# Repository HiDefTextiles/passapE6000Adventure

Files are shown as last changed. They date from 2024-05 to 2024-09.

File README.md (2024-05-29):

# Passap gögn
Kortlagning í formi dagbóka færslna af samasöfnuðum gögnum fræa veraldar vefnum.

Það eru tvennir hugar í þessum heimi:
* Croucher og Knitterstream.
	*	Hlaða inn .cut skrám með hámarkslengd og breidd
	*	Interface svo við consolið til að ná automation
* Bamberg og Irene.
	*	Fjarlægja consolið og tengja allt í arduino
	*	Lesa staðsetningu frá ljósa skynjurum
	*	Stýra nálum sjálf með innbygðu seglunum
Sjá dagbók hér að neðan.

# Passap E6000

# 2/5/24

Samskipti helgu við Chris ofthestreet og
Annacroucher
## TODO, Hvað er?
* WinCrea
* KnitterStream
* DIN port
* Hvaða útgáfu erum við með?

<!-- `Creating our own circuit board, since arduino is too bulky and attaching that into the console` -->

### DIN port
Í tölvupóstasamskiptum er mynd þar sem sýnt er 6 pin DIN port.
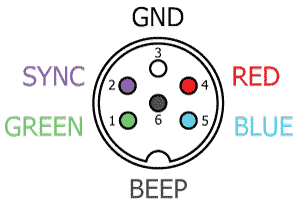
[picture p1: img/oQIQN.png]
Mynd af din 6 pin connector tengjum


### WinCrea
forrit til að gera hannanir fyrir Passap e6000 outputar .cut fileum sem er síðan hægt að h
### KnitterStream
* Notast við arduino til að interface við takka á stýringu.
* Hleður inn skrám eins og hægt er í chipset 23+ 

### Hvaða útgáfu erum við með?

Croucher vill að maður viti hvaða chipset vélin hefur en lýsingar til að komast að því eru óskýrar og krefjast jafnvel þess að rífa hana í sundur sem ég hef ekki leyfi fyrir enn.

## Chipset test
[Diana Natters umfjöllun um passap e6000](https://diananatters.blogspot.com/2010/10/passap-e6000-battery-chipset.html)

If it says MEMO, then start at step 1.

Þegar vélin er ræst kemur upp MEMO

Vélin öskrar og við fáum error 213.

Hún getur því ekki tekið við niðurhöluðum skrám.

## Croucher

Við erum með id 7041398 > 7037001.
Skv skjölum frá croucher eigum við því að vera með download og 32kb minni. En testið sem ég gerði frá diönu gaf error 213. Las yfir documentation fræa croucher aftur og hann seigir að error 213 sé rétt. Rámaði í það að ég hefði séð þessa tölu áður. Diana skrifar óskýrt en þetta er þá komið núna. Við erum með stuðning við að downloada patternum.

Það eru til mismunandi týpur af vélinni.
Það var bætt við download support frá MSDOS og auka minni í nýrri vélunum.
Það er hægt að uppfæra í það og kaupa frá honum íhluti til þess. Hann mæli eindregi með því að maður leggji ekki í það að uppfæra minnið og virðast ekki vera miklir kostir til þess.

Hægt er að hlaða niður skjölum, .cut sem innihalda
leiðbeiningar um lita munstur upp að 4 litum.
0,1,2,3
Leiðbeiningar um uppsetningar slíkar skrár eru í skjölum sem croucher sendi.

Það skjal inniheldur header með 10 stöfum og svo munstrið.

* Litafjölda stafur [0,3,4]: HEX[30,33,34] = [1-2,3,4] Litir
* Bil: HEX[20]
* Breidd munsturs/dálkar á bilinu [bil,bil,1] til [1,8,0]
* Bil
* Lengd munsturs/raðir á bilinu [bil,bil,1] til [2,5,5]
* Bil
* Litamunstur þar sem hver tala merkir lit 0-3

Hef það á tilfinningunni að við séum með eldri týpu annars væri ég ekki að lesa tölvupósta frá 2014.

## Irene
[Irene](https://hackaday.io/project/163701-passap-e6000-rebuilt-and-replaced-console/details)
[Irene repo](https://github.com/IrenePassap/Passap-E6000-hacked-and-rebuilt/blob/master/Passap_Projekt_Raspberry_Pi_Version_36.3_23.7.21.py)

Hún notar eina raspberry pi sem stýrir svo þrem arduino vélum. ein fyrir motor til að færa fram og til baka, ein fyrir fremri 'lock' til að prjóna og aðra fyrir aftari 'lock'.

Hún er búin að breyta vélinni þannig að aftara borðið er eins og fremra og getur þá líka prjónað eh meira fancy.

Hún vitnar í [bamberg](https://www.hackerspace-bamberg.de/Passap_pfaff_e6000)
.

Bamberg talar 'lightbarriers' í "carriage" til að vita staðsetninguna.

Finnst líklegt að við þurfum bara einfaldlega að losta okkur við upprunalgeu stýringuna eins og aðrir hafa gert. Þá kemur upp vandamál Croucher um að þú þarft í raun að forrita allt frá grunni með mikilli vitneskju um prjón og vélbúnaðinn.

## Niðurstöður // Summary

Erum með stuðning við að downloada .cut fileum.

Höfum 32k chip en 20k minni skv nýtni áætlun croucher.

Irene og bamberg hafa fjarlægt consolið gjörsamlega og smíðað sitt eigið með raspberry pi.

Ég held að við viljum halda consolinu og allri tækninni þar inni. grf.

Spurning um að bæta þá ofaná eh stýringu sem interfacer við consolið. Skoða knitterstream betur.

# 3/5/24

Byrjum á að skoða Irene og Bamberg betur.

* [Bamberg Github](https://github.com/knitty/firmware/tree/master/software/Knitty)
* [Bamberg lýsing (þýsk)](https://www.hackerspace-bamberg.de/Passap_pfaff_e6000)
* [Irene Github](https://github.com/IrenePassap/Passap-E6000-hacked-and-rebuilt)
* [Irene dagbók](https://hackaday.io/project/163701-passap-e6000-rebuilt-and-replaced-console/details)

## Diagram
### Bamberg

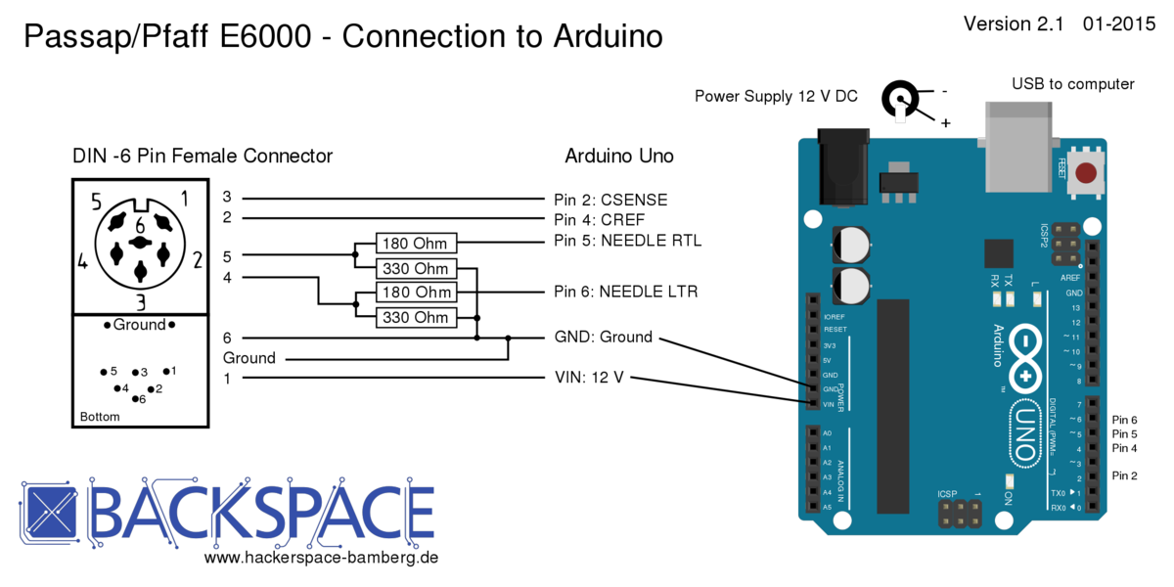
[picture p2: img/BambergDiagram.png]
BambergDiargram

Arduino unoinn kemur í stað stýringarinar 'consolsins' og notast þeir við sitt eigið forrit sem þeir gerðu fyrir alíka vél sem heitir [knitty](https://www.hackerspace-bamberg.de/Knitty)

Þeir eru líka með sér arduino fyror Autocolor, hvort hann hafi verið eh bilaður hjá þeim. Sé þetta ekki hjá Irene

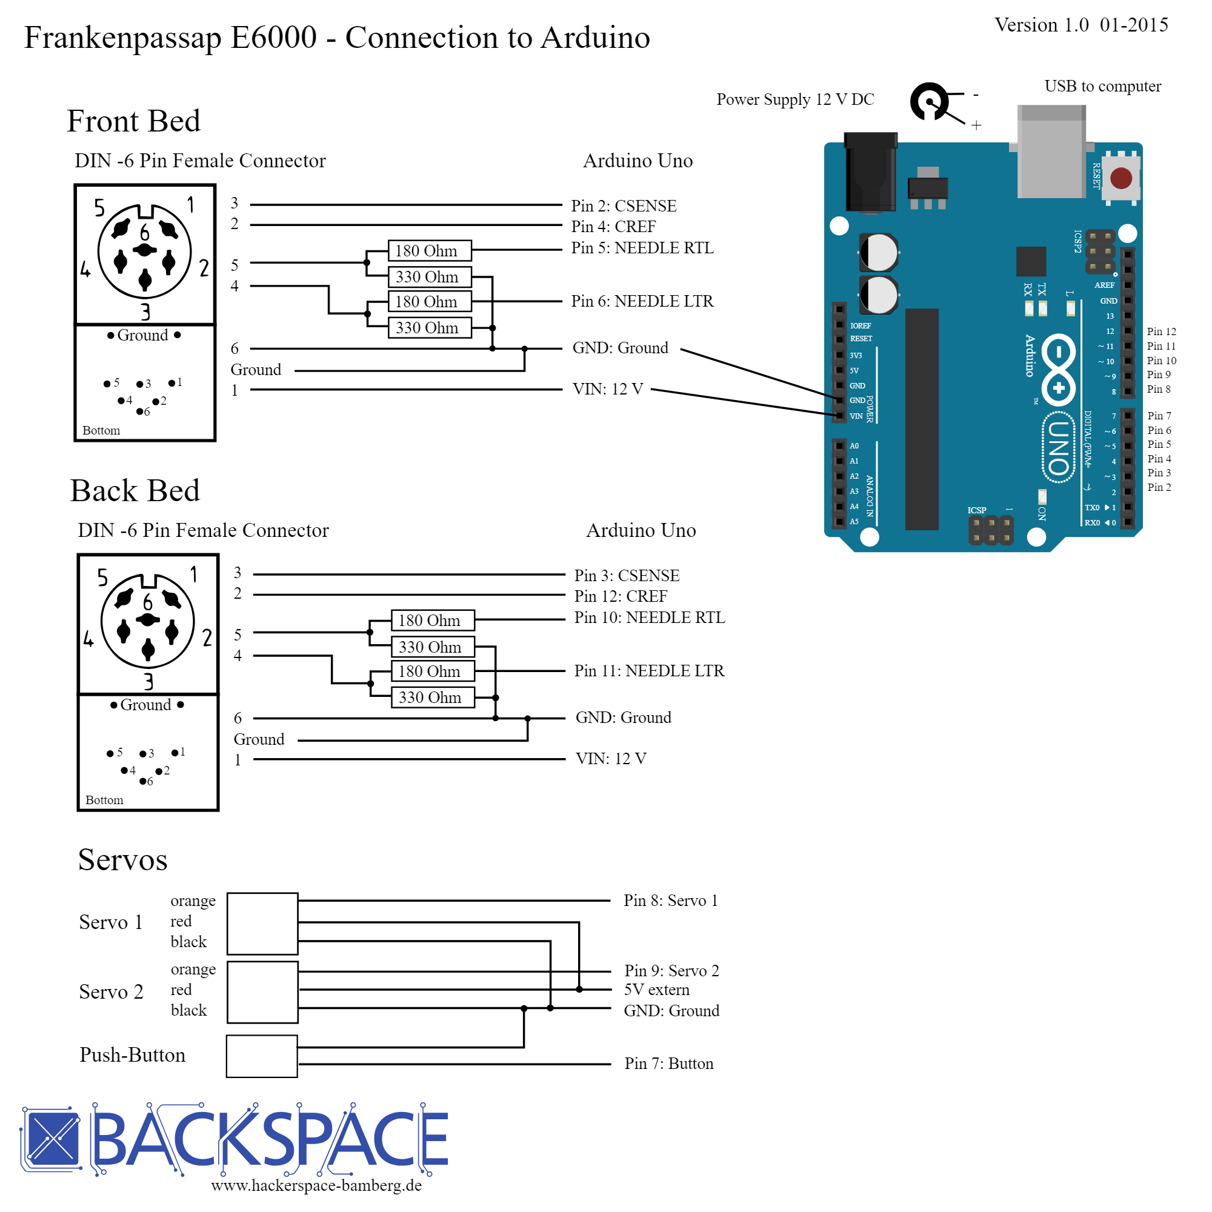
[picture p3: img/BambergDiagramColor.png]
mynd af tengingum við servo sem stýra litaskiptingum


[`Hægt er að sjá .svg diagram myndir frá Bamberg`](https://github.com/knitty/firmware/tree/master/hardware)

### Irene
IreneDiagram
Irene byggir á Bamberg en í stað þess að vera með tölvu usb tengda í arduino uno þá er raspberry pi með notendaviðmót sem stýrir

Lesa kóðan þeirra og skilja hvernig þau eru að lesa inn staðsetningu með pinum frá ljósunum. Þetta virðist ekki flókið en erfitt að ná hausnum almennilega utanum þetta án  þess að fikta sjálfur.
Mynd af seglum frá itene
<a href="https://hackaday.io/project/163701-passap-e6000-rebuilt-and-replaced-console/details" style="text-align:center;">Sjá meira hjá Irene</a>
Light sensorinn skýnir ljósi í 2mm göt á guiderail, 3mm á milli gata, 5mm er ein nál.

út frá munstri er hægt að lesa staðsetningu og átt lásins.

Ég bætti við Repoinu hennar Irene og bamber hér í möppu, til að auðvelda mér að fina efnið og rýna í það.

# 6/5/24

## Irene
Raspberry with two arduino sem stýra sitthvorum lásnum.
Hann stýrir svo mótornum. Það er ekkert samband á milli mótors og lása.

Mótorinn ýtir lásonum fram og til baka eins og ef noandi væri að gera það með hendinni og
lásarnir eru með ljós skynjara sem þeir nota til að lesa átt og staðsetningu.

Irene notast við technique.txt skrár fyrir gerð af prjóni?
Sva aðra skrá fyrir pattern.

Kóðarnir hennar eru torlesnir og gætu verið mun betur skrifaðir. Allar breytur eru global. Numpy er ekki notað fyrir fylki heldur forlykkju viðbjóður.

Ég tek það á mig að fara í gegnum þetta línu fyrir línu og endurskrifa allavega python kóðan uppá skilning fyrir mig. Besta leiðin til að skilja eitthvað er að laga það.

Þetta endar alltaf á því að maður þarf að fikta og prufa sig áfram.

Ég er búin að minnka fyrstu 800 línurnar niðu í minna en 200 með einfaldri notkun á numpy og skilning a fylkja notkun. Hægt er að sjá hreinskrifuðu útgáfuna undir möppunni Irene með nafninu controler-elli-cleanup.py

ég held áfram með þetta á morgun eftir hreinsun á vél

# 7/5/24

Þrif og teambonding

# 8/5/24

Punktar um gpio merki.

Til að fá gpio input í program er hægt að framkvæma "polling".
Getur misst af inputi ef gidli er lesið á vitlausum tíma.
Gert í lykkjum og er mögulega íþungt á keyrslu umhvefið.
Öunnr aðferðir er að nota "interrupts" sem tekur eftir muninum á milli breytingum, frá hi to low (falling) frá low to hi (rising)

Kláruðum að þrífa.

Skoðaði betur munninn á tölvu og mekanísku útgáfunni frá Passap.

Tölvu útgáfan er með 
- 2 input, ljósskynjararnit tveir sem staðsetjan
- 2 output, seglar sem raða nálum fyrir munstur næstu línu
Sameiginlegt er
- Mekaníkinn sem ýtir nálonum upp er sú sama.
- nálabeðið er óbreytt

# 10/5/24

Öll ljós slökkt og ekki sál að sjá.

Er komin með 250 línur af hreinskrifaðari kóða útgáfu frá Irene.

Er að bryja á tech array hjá henni.

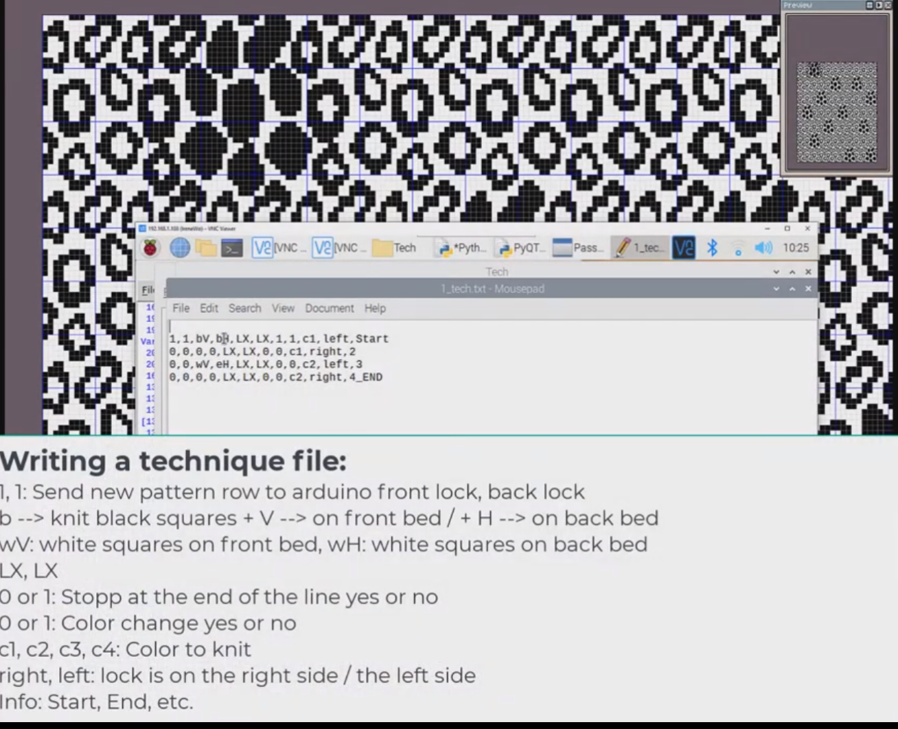
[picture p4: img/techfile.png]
Mynd af tech array dæmi


Hér útskýrist betur þessi blessaði tech array file hjá henni.

fyrstu tvö gildin lýsir hún sem skipun um að byrja pattern á nýrri línu.

```
    x = tech_Array[countTech][0]
    x = int(x)
    rowCount_VNB = int(rowCount_VNB) + x
```

Þar sem rowcount_VNB er nr línu á fremri lásnum.
countTech er lína í tech file, 0 er index á fyrstu tölunni

Næst koma hvaða lita vigra hún nota.
Þar er gefin strengur sem er enumaður á skipun sem sendir viðeigandi vigur á viðeigandi Arduino.

V - fremri, H - Aftari

Svo er stillingin sem að lásin á að vera í. Hún stilir það sjálf

svo skipanir til að skipta um lit, sem ég skil ekki alveg.

Hún seigir að þetta sé boolean já og nei fyrir skipti og stop en þegar hún skiptir um lit breytast þesssi gildi ekki neitt.

svo bara info dump, þetta væri vel hægt að sleppa.

Virkni segla lásins voru í raun sanreynd í prufunum í dag. 
Hann stillit uppröðunninni fyrir næstu umferð. Default er 1 þarf að senda 0 til að setja í hvildarstöðu.
Pusherarnir stýra svo einhvernveginn hvaða nálar eru notaðar.
Það er bara hlustað á pusherana þegar x stilling er virk og þegar kveikr er á örvum í gömlutýpunni er uppröðun þeirra breytt.

Þetta væri þá hægt að þýða yfir í kóða og sleppa motor stýringum.

Prufurnar gengu þó eh og gott að sjá mekaníkinn í virkni.

# 15/5/24

## Prototype 1

Staðan í dag, komin með arduino tengingu við lásinn. Get lesið ljósskynjara og breytt segulsviði seglana.

Þá er bara að stúttera bamberg og irene stýringarnar.

Næ að láta intterupt virka fyrir PIN_CSENSE en ekki PIN_CREF, en hann skynjar breytt gildi á báðum þannig við látum eina innterrupt rútínu virka

Fyrir Vinstri til hægri koma gildin

40 & 31

Fyrir hægri til vinstri fáum við gildin

41 & 30

Úr innterrupt rútinum hennar Irene

# 16/5/24

## Prototype 2
Ný rás fræsuð, viðnám lóðuð, tengi og pinnar.

Skynjarar í lagi, skipti út powersupply fyrir annað sem ég fann liggjandi í vr 3 og seglarnir virka.

Þá er bara eftir að útfæra kóða sem samnýtir hreyfingu

# 17/5/24

CREF er ekki tengt í pinna sem styður interrupt.

Vélin stíflaðist, tók hana í sundur, sem er fínt. Hafði langað að gera það til að sjá pusherana betur.

# 21/5/24

Horfði upp undir pusherana til að sjá hvar þeir byrja að raðast eftir stillingu. Breytti svo stillingunni og sá hversu margir pusherar voru á milli þess að breytinginn skilaði sér. Merkti þann punkt á velina og notaði hann sem calibration punkt.

Þetta er punkturinn þar sem röðun pusherana er ákveðin. Hvort þeir fara upp eða niður. Miðaði svo við þann punkt og prófaði að færa hann eitt nálarbeð í einu og breyta stillingu til að sannreyna og það gekk. 

Notaði svo ljósaskynjarann og las hvaða munstur kom úr interruptinu í hvert skipti sem ég færði calibration/samstillingar punktinn á milli nálarbeða. 

Tölugildin eru því 41 og 31 eða 11 og 01;
11: Cref=1 & Csense=1;
01: Cref=0 & Csense=1;

Til að staðsetja lásin á nálarbeðinu tökum við hann alveg út í enda. Rennum honum svo hægt inná leiðarvísirinn og greinum gildi.

Út frá því fáum við alla punkta. Það ætti að vera nóg að gera þetta bara í eina átt. Frá vinstri til hægri, horft beint á fremri lásin. Því Hægri til vinstri ætti í raun bara að telja niður sömu gildi, allavega fyrir nálarbeðin, jaðar punktarnir gætu verið annað mál. SKoðum það þegar þar að kemur

Punktar fyrir kvörðun á nálabeða ás útfrá ljósskynjara

Upphafsgildi breyturnar state & counter eru 0;
```
// direction
volatile int state = 0;
// position
volatile int counter = 0;
```

State seigir okkur um stöðu beggja ljósskynjarana og útfrá því getum við ákvarðað átt. Counter telur hverja nál og er ætlað til að staðsetja okkur.

Með state ákvöðrum við hvort við hækkum eða lækkum counter, út frá counter fáum við staðetningu

# 22/5/24

Villur lagaðar og ás nálabeðs kvarðaður.

Til að kvarða nálabeðið þarf að taka lásinn/sleðann af. Endurkveikja á arduino og renna honum á.

// 30 0
// 31 0

// 31 0
// 40 -1
// 41 0
// 40 -1
// 41 0
// 40 -1

// byrjar 31 0
// svo mynztur 40 - 41
// byrjar loks 41 - 30
// í 28 erum við komin á fyrstu nálina
// 207 seinasta nál || 206
// 243 auto color endir
// 221 útaf hægri

# 23/5/24

Munztrið sem kemur þegar honum er rennt á er, 40 telur niður og 41 upp

31 - 0
40 - -1
41 - 0
40 - -1
41 - 0
40 - -1
41 - 0 // 41-30 nála munustur++
30 - 0
41 - 1

28 er nál 1 og 206 nál 179

## Kenning 

Nálabeðið er samhverft og merkt með heiltölum í báðar áttir frá miðju með 

90 nálar vinstra megin

89 nálar hægra megin

Tölvur byrja í núlli, þannig ef fyrsta nálinn vinstra megin við miðju er 0
þá er nálabeðið samhverft um hana í hugbúnaðinum það er

-89 0 89.

## Framkvæmd

Við viljum að notandinn geti skilgreint fyrstu nál til vinstri. Best væri að notandinn gæti notast við innbygpu tölurnar á vélinni.

Notandi segir að munztur byrji á nál 90 til vinstri, þá þarf það að vera 0 í munztur vigri.

setur inn -90,
sem er nál 28
### Hugmynd
```
int input = -90;
int start = (input < 0) ? input +90 : input + 89;
int line = 0;
counter - 28 - (start) = 0;
206 - 28 = 179
if (counter >= (28+start) && counter < 207)
{
	int index = counter - 28 - start;
	digitalWrite(pin,PatternMatrix[index])
	if (counter > width of matrix + start || (line>0 && counter < 28+start))
	{
		line++
	}
}

counter - 28 + input = 0
```

### útfærsla
Notobene þetta eru 178 nálar og við byrjum í 0,
þannig index er á bilinu 0-177, fyrir allar nálar á borðinu

#### Einn vídd Index
```
    int input = -90;
    int start = (input < 0) ? input + 90 : input + 89;
    int index = counter - 28 - start;
```
If var óþarfi þar sem við setjum bara núll punkt og okkur ætti að vera sama um öll önnur gildi. Þannig þótt index flæði út fyrir þá er hann ekki að stýra neinu.

Þegar ég var að prufukeyra index, var ljost að þar sem seglarnir eru ekki á samastað þá þarf að vera með sér tölu fyrir hvorn, það virðist vera 10 nála bil á milli, þannig við bara bætum við 10 á bakaleiðinni við index. einnig virtist vera 2 nála offset frá fyrstu nál og stillingar punkti, sem er innan skekkju marka mannsins.

vona ég.

ég breytti því núll punkti nálarásins í 26 til að lagfæra það.

```
		int input = -10;
		int start = (input < 0) ? input + 90 : input + 89;
		int index = counter - 26 - start;
		int value = 1;
```
##### Hægri til vinstri
```
			if (index + 10 >= 0 && index + 10 < arraysize)
			{
				value = array[index + 10];
			}
			digitalWrite(PIN_NEEDLE_RTL, value);
```
##### Vinstri til hægri
```
			if (index >= 0 && index < arraysize)
			{
				value = array[index];
			}
			digitalWrite(PIN_NEEDLE_LTR, value);

```
#### Tveggja vídda Index
Þá er það línu meðhöndlun.

Byrjum alltaf að prjóna hægri til vinstri.
Setjum alltaf lásinn/sleðann á frá vinstri til hægri.

Þurfum þá að stilla nálarnar þannig fyrst.

Þannig sleðin byrjar alltaf lengst til vinstri?
vonandi

# 27/5/24

Fann kennslumyndbönd á netinu um það hvernig maður sendir skipanir frá python yfir á arduino.

## Næstu ítranir // TODO
- Útfæra grunn að samskiptum á milli arduino og umheimsins
	- Bæta við raspberry pi
	- bakenda
	- python/javascript?
- Bæta við motor // skoða
	- mögulega motor stýringu
	- Hægt að vita staðsetningu autocolor

# 28/5/24

Takmarkanir á gögnum send til arduino.

Ef við notum streng þá getur hann verip með 768 stafi.

Ef við sendjum

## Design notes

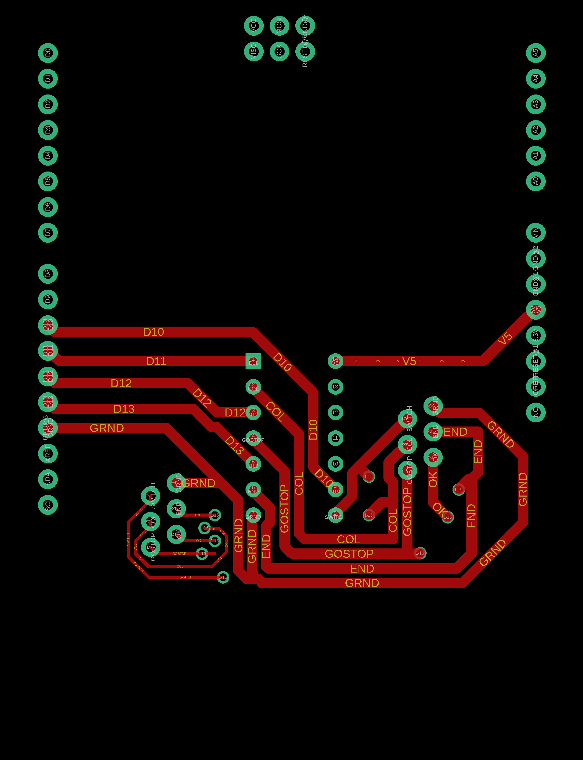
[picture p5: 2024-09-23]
teikningarRaf/Passap/PASSAP_MOTOR_ARDUINO.png

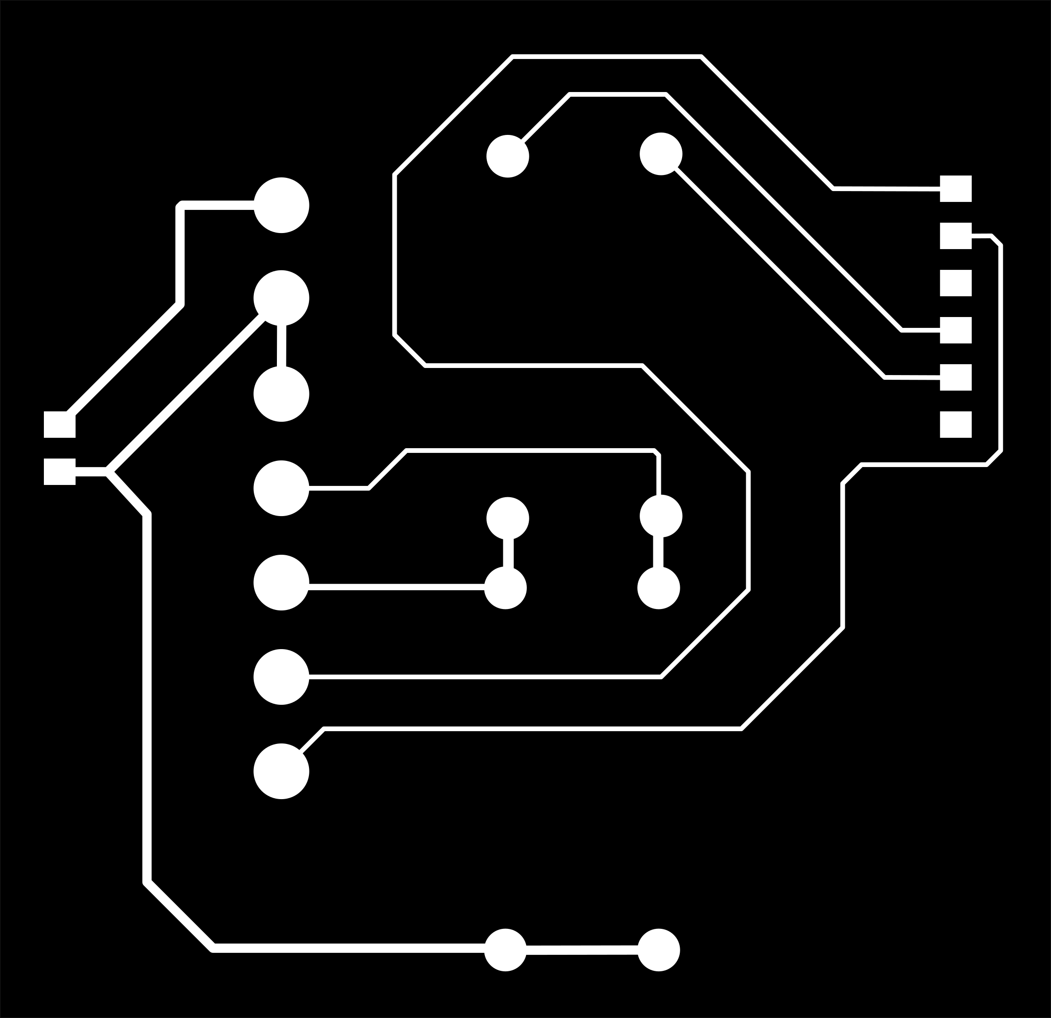
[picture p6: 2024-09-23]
teikningarRaf/svgdot/Traces.png

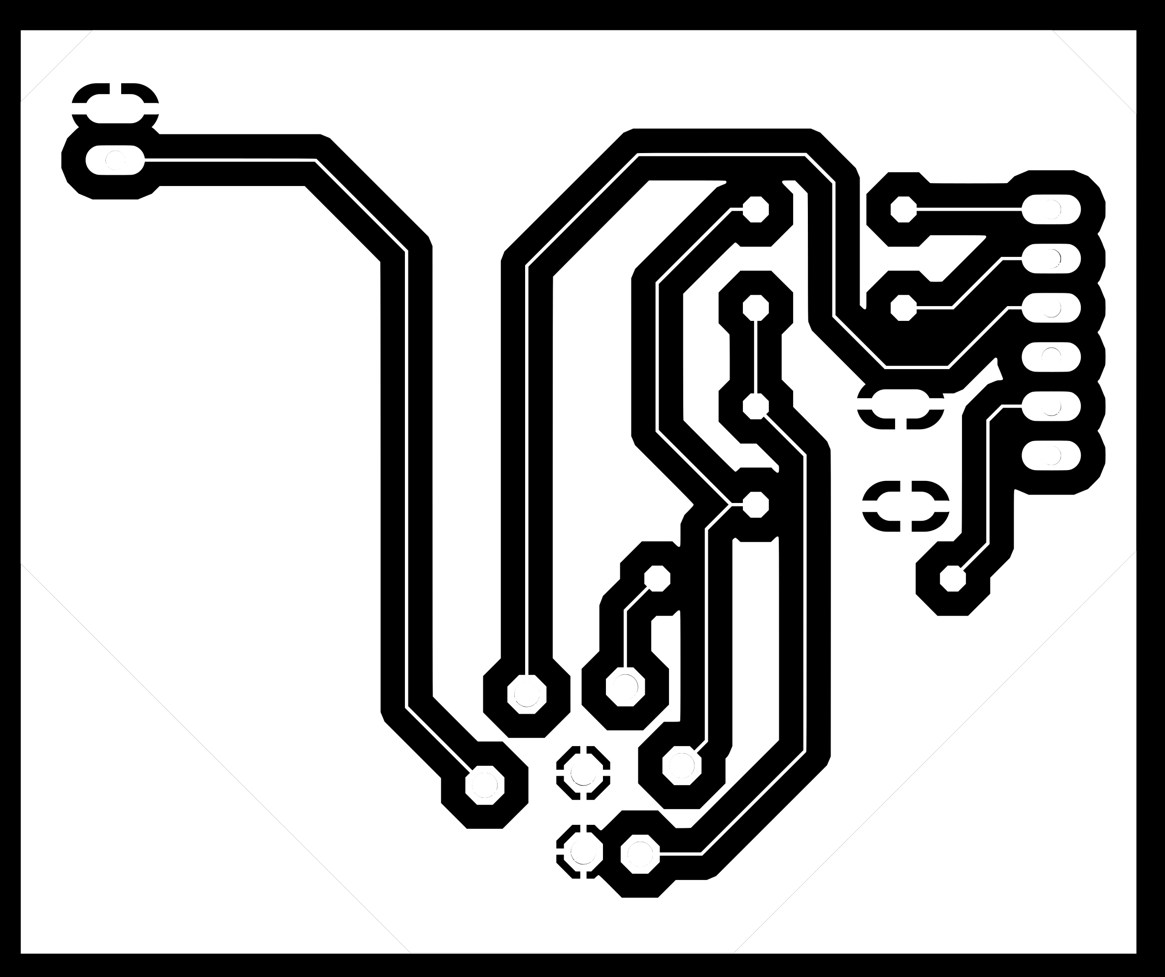
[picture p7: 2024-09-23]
teikningarRaf/svgdot/Traces_Thundercat.png

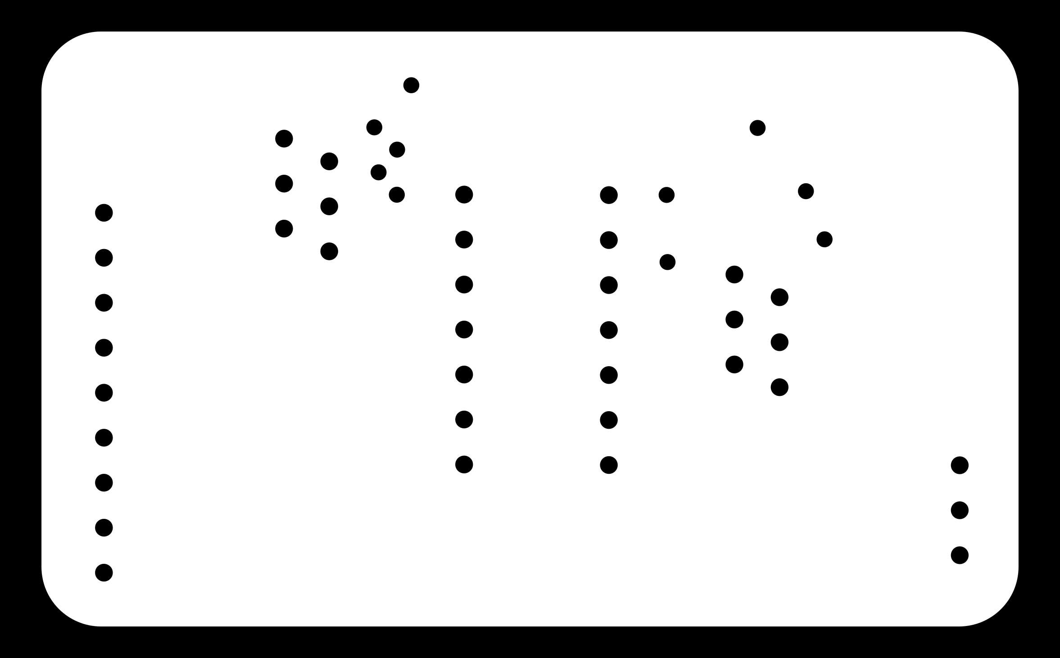
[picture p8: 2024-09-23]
teikningarRaf/svgdot/PassapMotorOutline1_flip.png

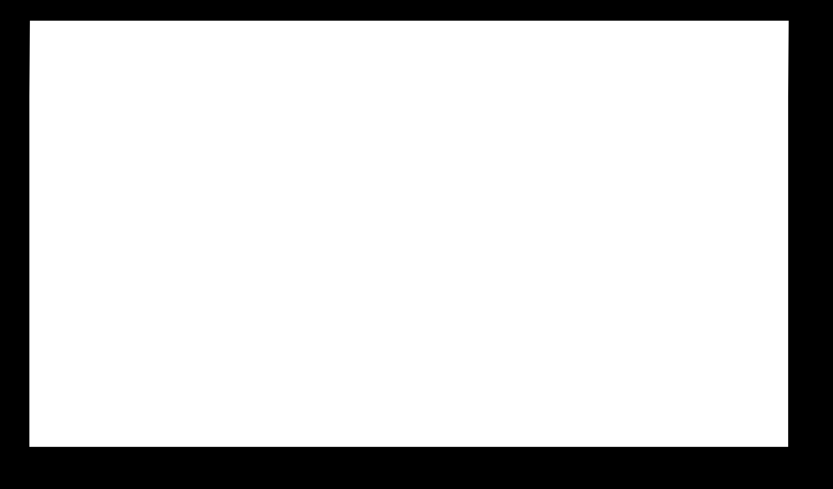
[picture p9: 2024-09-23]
teikningarRaf/svgdot/passapMotorKassi.png

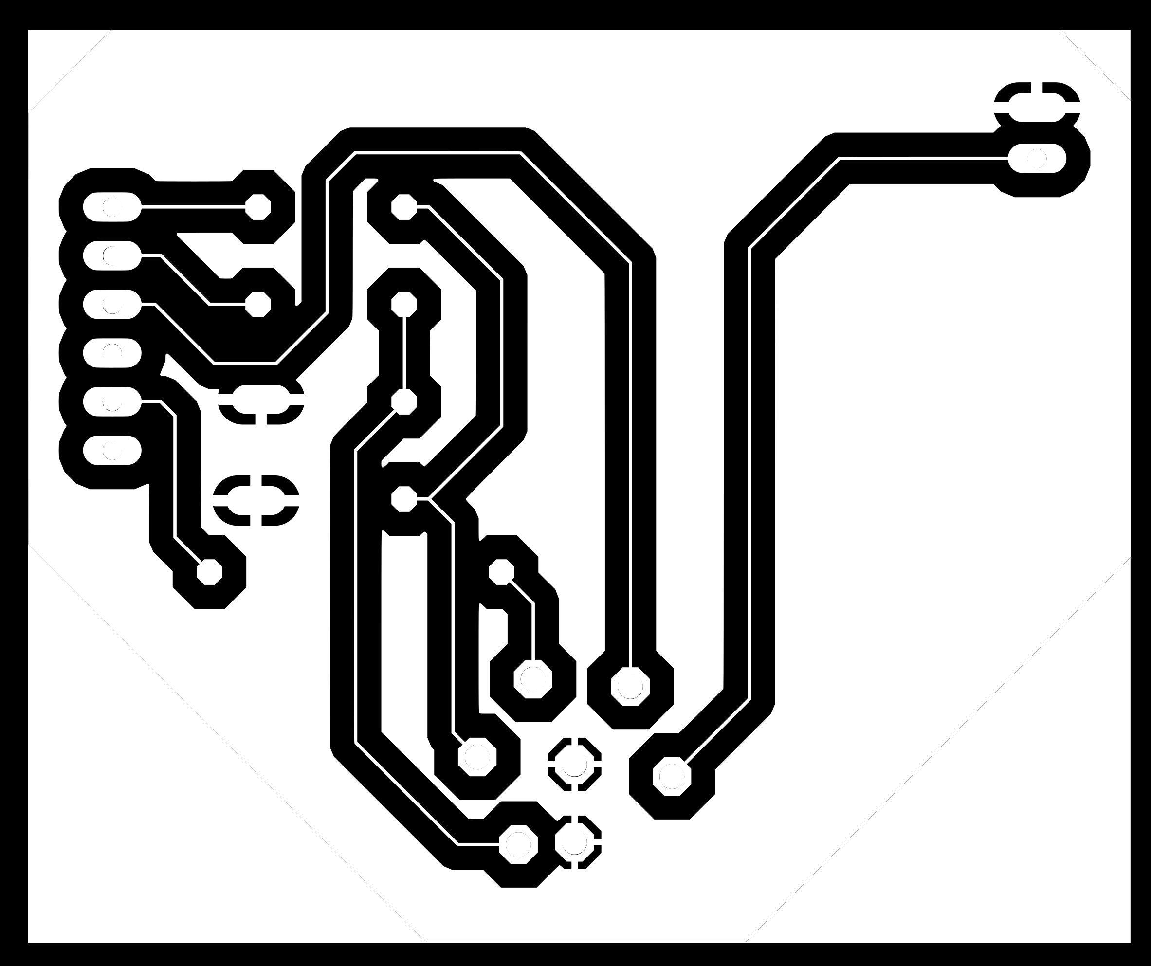
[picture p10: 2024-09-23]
teikningarRaf/svgdot/Traces+thundercat1.png

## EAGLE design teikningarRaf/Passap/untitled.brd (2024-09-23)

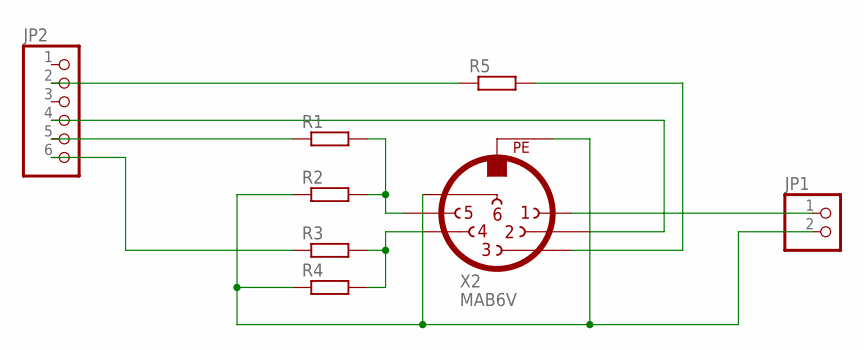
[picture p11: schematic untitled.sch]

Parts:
JP1: PINHD-1X2; 1X02
JP2: PINHD-1X6; 1X06
R1, R2, R3, R4: R-EU_0204/7; 0204/7
R5: R-EU_0207/15; 0207/15
X2: MAB6V

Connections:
GND: JP1.2, R2.1, R4.1, X2.6, X2.PE
unnamed: R1.2, R2.2, X2.5
unnamed: R3.2, R4.2, X2.4
unnamed: R5.2, X2.3
unnamed: JP2.5, R1.1
unnamed: JP2.6, R3.1
unnamed: JP2.4, X2.2
unnamed: JP2.2, R5.1
unnamed: JP1.1, X2.1

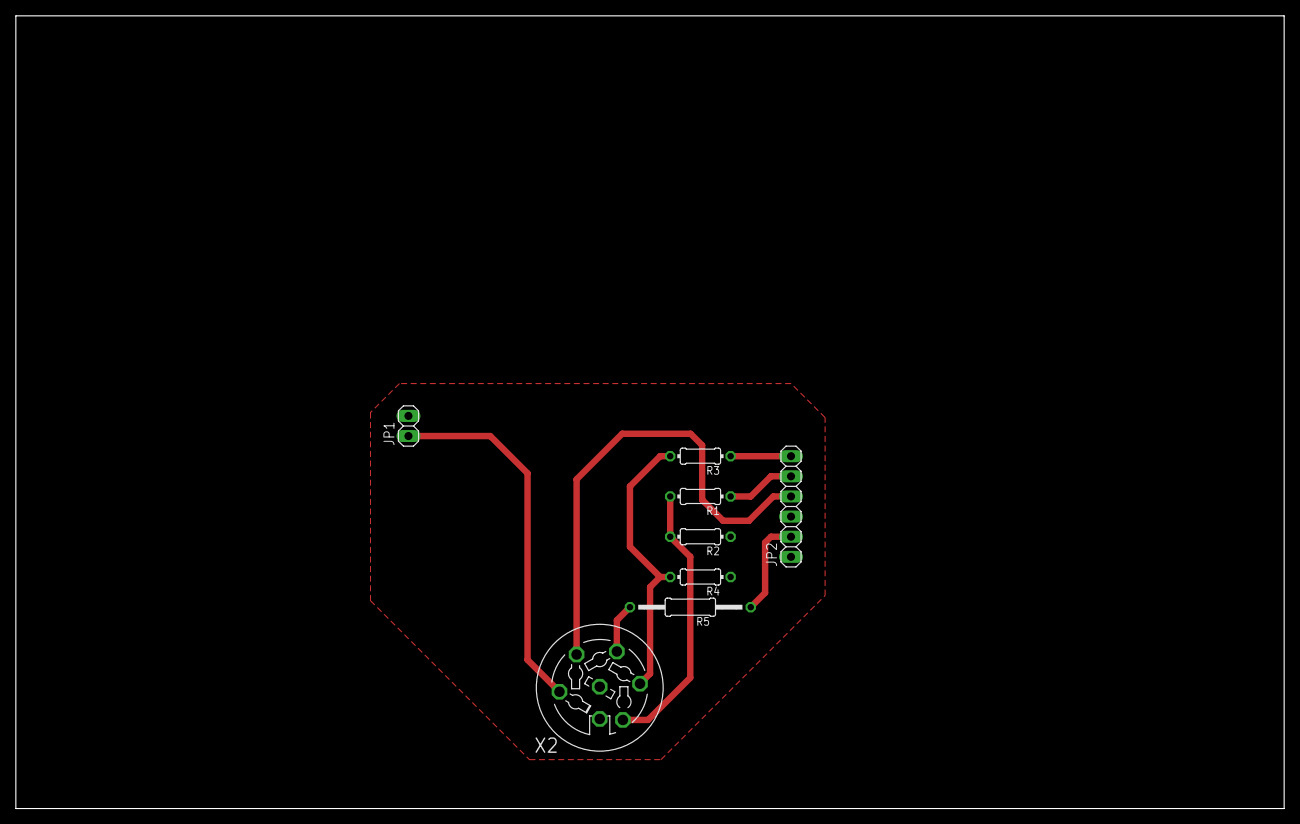
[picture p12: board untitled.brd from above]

Board: 2 copper layers, 160.0 x 100.0 mm, 8 parts (0 on the bottom side), 9 nets.

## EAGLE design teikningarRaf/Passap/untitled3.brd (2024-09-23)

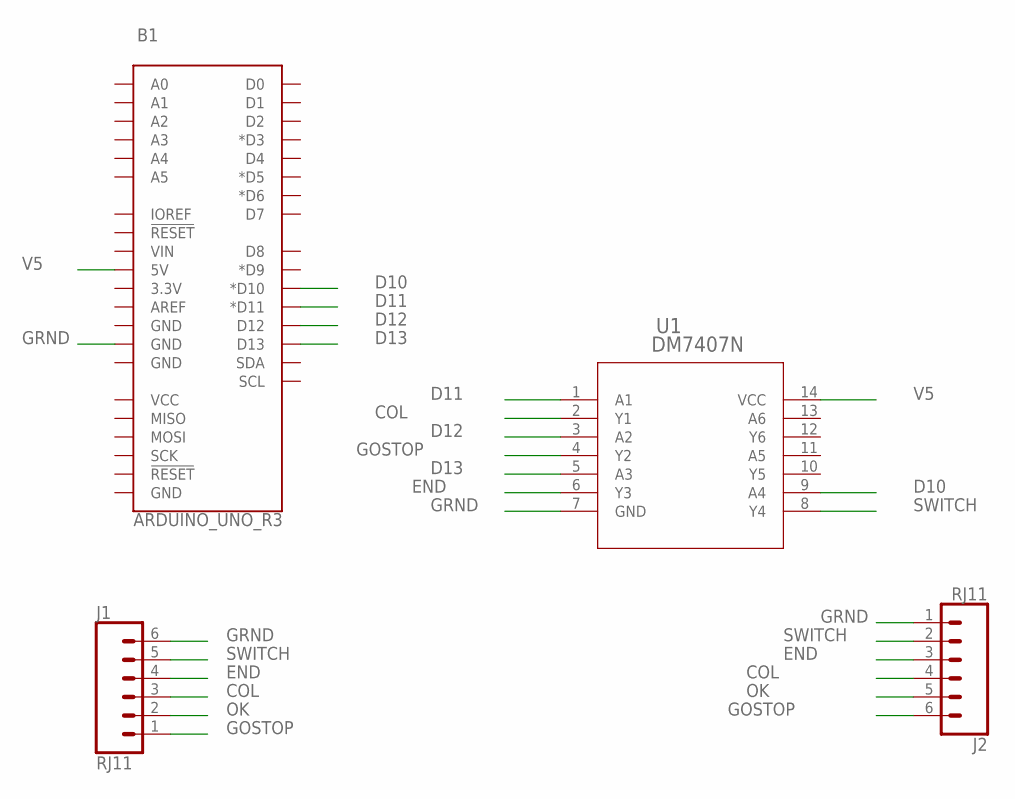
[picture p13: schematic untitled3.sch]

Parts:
B1: ARDUINO_UNO_R3; ARDUINO_R3
J1, J2: RJ11; RJ11-6
U1: DM7407N; PDIP14_6P35X19P56_ONS

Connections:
COL: J1.3, J2.4, U1.2 (Y1)
D10: B1.D10 (*D10), U1.9 (A4)
D11: B1.D11 (*D11), U1.1 (A1)
D12: B1.D12, U1.3 (A2)
D13: B1.D13, U1.5 (A3)
END: J1.4, J2.3, U1.6 (Y3)
GOSTOP: J1.1, J2.6, U1.4 (Y2)
GRND: B1.GND@3 (GND), J1.6, J2.1, U1.7 (GND)
OK: J1.2, J2.5
SWITCH: J1.5, J2.2, U1.8 (Y4)
V5: B1.5V, U1.14 (VCC)

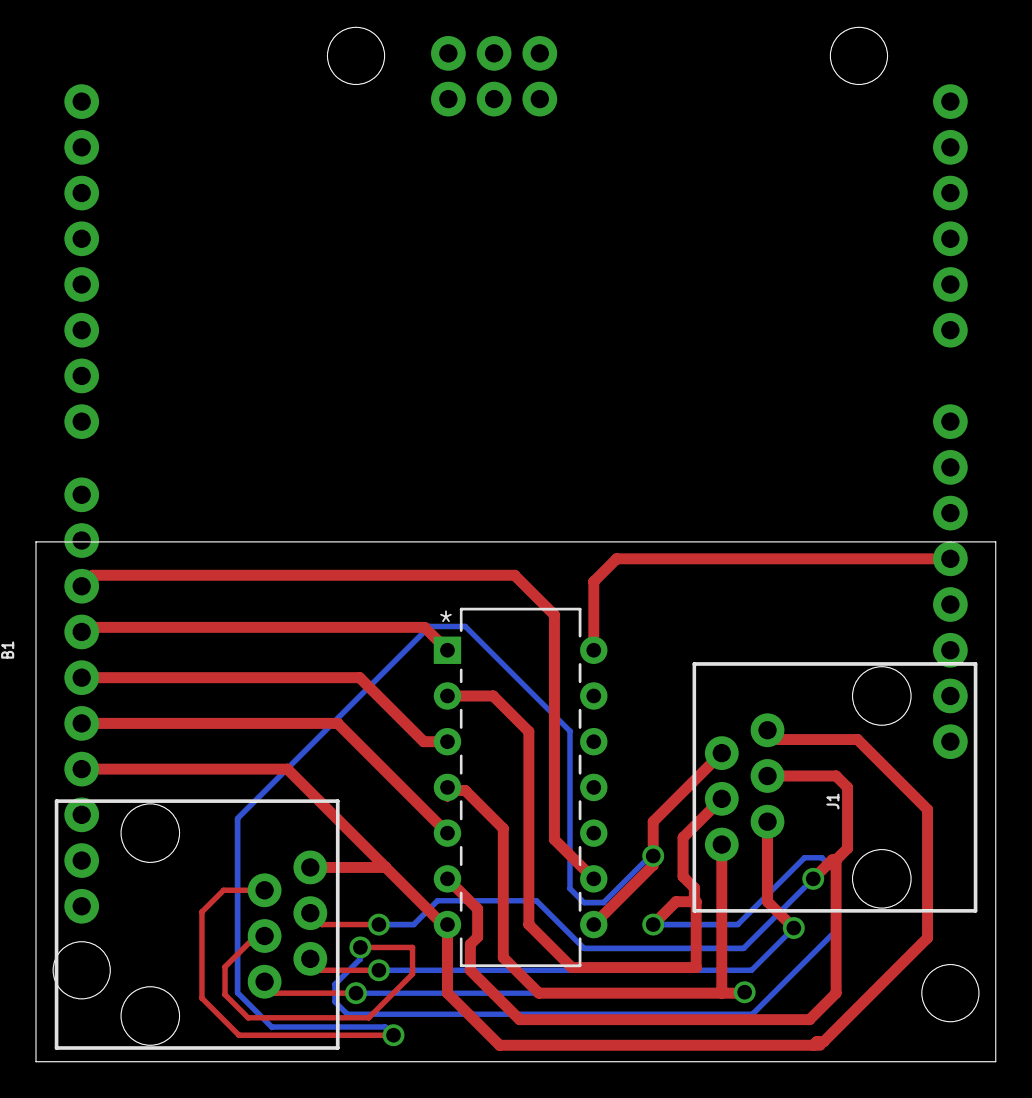
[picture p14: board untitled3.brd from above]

Board: 2 copper layers, 53.3 x 28.9 mm, 4 parts (0 on the bottom side), 11 nets.

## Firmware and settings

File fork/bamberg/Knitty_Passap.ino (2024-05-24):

//////////////////////////////////////////////////////////////////////////////
// Knitty Project
// Arduino Firmware for Passap E6000
//
// Author: ptflea, schinken,
//
// version 2015-10-05

// Servo
#include <Servo.h>

Servo servoColour12; // create servo object to control a servo
Servo servoColour34;

// define interupts for CSENSE
#define INT_ENCODER 0
#define INT_ENCODER_BACK 1

//////////////////////////////////////////////////////////////////////////////
// General purpose definitions

// front carriage
#define PIN_CSENSE 2     // Yellow
#define PIN_CREF 4       // White
#define PIN_NEEDLE_RTL 5 // Blue,  Pattern RTL
#define PIN_NEEDLE_LTR 6 // ,  Pattern LTR
// back carriage
#define PIN_CSENSE_BACK 3      //
#define PIN_CREF_BACK 12       //
#define PIN_NEEDLE_RTL_BACK 11 //   Pattern RTL
#define PIN_NEEDLE_LTR_BACK 10 //   Pattern LTR

// PIN 8 and 9 are for the color change servos

#define DIRECTION_UNKNOWN 0
#define DIRECTION_LEFT_RIGHT -1
#define DIRECTION_RIGHT_LEFT 1

#define DIRECTION_UNKNOWN_BACK 0
#define DIRECTION_LEFT_RIGHT_BACK -1
#define DIRECTION_RIGHT_LEFT_BACK 1

char currentDirection = DIRECTION_UNKNOWN;
char lastDirection = DIRECTION_UNKNOWN;
char currentDirection_back = DIRECTION_UNKNOWN;
char lastDirection_back = DIRECTION_UNKNOWN;

signed int currentCursorPosition = 0;
unsigned long lastCursorChange = 0;
unsigned int currentPatternIndex = 0;
signed int firstNeedle = 0;
signed int offsetCarriage_RTL = 53;
signed int offsetCarriage_LTR = 29;

signed int currentCursorPosition_back = 0;
unsigned long lastCursorChange_back = 0;
unsigned int currentPatternIndex_back = 0;
// signed int firstNeedle_back = 0;
signed int offsetCarriage_RTL_back = 50;
signed int offsetCarriage_LTR_back = 27;

int knitPattern[255] = {0};
int knitPattern_back[255] = {0};

int passapCalibrateArray[8] = {0};
signed int passapCalibratePointer = 0;
static unsigned char passaptestpattern[8] = {1, 0, 1, 1, 0, 0, 0, 1};

int passapCalibrateArrayBack[8] = {0};
signed int passapCalibratePointerBack = 0;
static unsigned char passaptestpatternBack[9] = {0, 0, 1, 1, 1, 0, 1, 1, 0};

char currentPinChangeValue = 0;
char currentPinChangeOppositeValue = 0;
char currentPinChangeValue_back = 0;
char currentPinChangeOppositeValue_back = 0;
signed int currentCursorPositionLast = 0;
signed int currentCursorPositionLast_back = 0;
//////////////////////////////////////////////////////////////////////////////
// Knitty Serial Protocol

// Receive commands
#define COM_CMD_PATTERN 'P'
#define COM_CMD_PATTERN_BACK 'B'
#define COM_CMD_PATTERN_END 'E'
#define COM_CMD_CURSOR 'C'
#define COM_CMD_RESPONSE 'R'
#define COM_CMD_DIRECTION 'D'
#define COM_CMD_DEBUG 'V'
#define COM_CMD_NEW_PATTERN 'N'
#define COM_CMD_FIRST_NEEDLE 'F' // first needle of pattern from right
#define COM_CMD_SEPERATOR ':'
#define COM_CMD_STATUS 'T'

#define COM_CMD_SERVO 'S'

#define COM_CMD_PLOAD_END '\n'

// Parser states
#define COM_PARSE_CMD 0x01
#define COM_PARSE_SEP 0x02
#define COM_PARSE_PLOAD 0x03

unsigned char parserState = COM_PARSE_CMD;

unsigned char parserReceivedCommand = 0;
String parserReceivedPayload = "";
unsigned char patternLength = 0;
unsigned char patternLengthBack = 0;

void setup()
{
  Serial.begin(115200);
  sendCommand(COM_CMD_RESPONSE, "up and running");

  // Setup PHOTO SENSOR pin change interrupt
  pinMode(PIN_CSENSE, INPUT_PULLUP);
  pinMode(PIN_CSENSE_BACK, INPUT_PULLUP);

  pinMode(PIN_CREF, INPUT_PULLUP);
  pinMode(PIN_CREF_BACK, INPUT_PULLUP);

  attachInterrupt(INT_ENCODER, interruptPinChangeEncoder, CHANGE);
  attachInterrupt(INT_ENCODER_BACK, interruptPinChangeEncoder_back, CHANGE);

  // Setup Needles
  pinMode(PIN_NEEDLE_RTL, OUTPUT);
  digitalWrite(PIN_NEEDLE_RTL, HIGH);
  pinMode(PIN_NEEDLE_LTR, OUTPUT);
  digitalWrite(PIN_NEEDLE_LTR, HIGH);

  pinMode(PIN_NEEDLE_RTL_BACK, OUTPUT);
  digitalWrite(PIN_NEEDLE_RTL_BACK, HIGH);
  pinMode(PIN_NEEDLE_LTR_BACK, OUTPUT);
  digitalWrite(PIN_NEEDLE_LTR_BACK, HIGH);
}

void loop()
{
  parserSerialStream();
  patternFront();
  patternBack();
}

void executeCommand(unsigned char cmd, String payload)
{

  switch (cmd)
  {
  case COM_CMD_PATTERN:
    // Serial.print("P ");
    // Serial.println(patternLength);
    //  sendCommand(COM_CMD_RESPONSE, "PatternLength: " + String(patternLength));
    break;

  case COM_CMD_PATTERN_BACK:
    // Serial.print("B ");
    // Serial.println(patternLengthBack);
    // sendCommand(COM_CMD_RESPONSE, "PatternLengthBack: " + String(patternLength));
    break;

  case COM_CMD_CURSOR:
    currentCursorPosition = payload.toInt();
    break;

  case COM_CMD_FIRST_NEEDLE:
    firstNeedle = payload.toInt() * 2 - 2;

    sendCommand(COM_CMD_RESPONSE, "FirstNeedle: " + String(firstNeedle));
    break;

  case COM_CMD_STATUS:
    sendCommand(COM_CMD_RESPONSE, "-------------------------");
    sendCommand(COM_CMD_RESPONSE, "Cursorposition: " + String(currentCursorPosition));
    sendCommand(COM_CMD_RESPONSE, "PatternIndex: " + String(currentPatternIndex));
    if (currentDirection == DIRECTION_RIGHT_LEFT)
    {
      sendCommand(COM_CMD_DIRECTION, "RTL");
    }
    else
    {
      sendCommand(COM_CMD_DIRECTION, "LTR");
    }
    sendCommand(COM_CMD_RESPONSE, "-------------------------");

    break;

  case COM_CMD_SERVO:

    switch (payload.toInt())
    {
    case 0: // no colour selected
      servoColour12.write(90);
      servoColour34.write(90);
      break;
    case 1: // Color 1
      servoColour12.write(70);
      servoColour34.write(90);
      break;
    case 2: // Color 2
      servoColour12.write(115);
      servoColour34.write(90);
      break;
    case 3: // Color 3
      servoColour12.write(90);
      servoColour34.write(70);
      break;
    case 4: // Color 4
      servoColour12.write(90);
      servoColour34.write(115);
      break;
    case 5: // Servo off
      servoColour12.detach();
      servoColour34.detach();
      break;
    case 6: // Servo on
      servoColour12.attach(8);
      servoColour34.attach(9);
      break;
    }

    break;
  }
}

void sendCommand(unsigned char cmd, String payload)
{
  Serial.write(cmd);
  Serial.write(COM_CMD_SEPERATOR);
  Serial.print(payload);
  Serial.write("\n");
}

void parserSerialStream()
{

  if (Serial.available() == 0)
  {
    return;
  }

  char buffer = Serial.read();

  switch (parserState)
  {

  case COM_PARSE_CMD:
    parserState = COM_PARSE_SEP;
    parserReceivedCommand = buffer;
    parserReceivedPayload = "";
    if (buffer == COM_CMD_PATTERN)
    {
      patternLength = 0;
    }

    if (buffer == COM_CMD_PATTERN_BACK)
    {
      patternLengthBack = 0;
    }
    break;

  case COM_PARSE_SEP:

    // We're awaiting a seperator here, if not, back to cmd
    if (buffer == COM_CMD_SEPERATOR)
    {
      parserState = COM_PARSE_PLOAD;
      break;
    }

    parserState = COM_PARSE_CMD;
    break;

  case COM_PARSE_PLOAD:

    if (buffer == COM_CMD_PLOAD_END)
    {

      executeCommand(parserReceivedCommand, parserReceivedPayload);
      parserState = COM_PARSE_CMD;

      ////sendCommand(COM_CMD_RESPONSE, "Received");
      break;
    }

    if (parserReceivedCommand == COM_CMD_PATTERN)
    {
      // Change state because the E6000 set the needle at '0'
      knitPattern[patternLength] = (buffer == '0') ? 1 : 0;
      // reverse pattern
      // knitPattern_back[patternLength] = (buffer == '1')? 1 : 0;

      // Serial.println(String(knitPattern_back[patternLength])+String(patternLength));
      patternLength += 1;
    }
    else if (parserReceivedCommand == COM_CMD_PATTERN_BACK)
    {
      // Change state because the E6000 set the needle at '0'
      knitPattern_back[patternLengthBack] = (buffer == '0') ? 1 : 0;
      // Serial.println(String(knitPattern_back[patternLength])+String(patternLength));
      patternLengthBack += 1;
    }
    else
    {
      parserReceivedPayload += buffer;
    }

    break;
  }
}

void setNeedle_RTL(char state)
{
  // Attention E6000 sets needle by 0
  digitalWrite(PIN_NEEDLE_RTL, state);
}

void setNeedle_RTL_back(char state)
{
  // Attention E6000 sets needle by 0
  digitalWrite(PIN_NEEDLE_RTL_BACK, state);
}

void setNeedle_LTR(char state)
{
  // Attention E6000 sets needle by 0
  digitalWrite(PIN_NEEDLE_LTR, state);
}

void setNeedle_LTR_back(char state)
{
  // Attention E6000 sets needle by 0
  digitalWrite(PIN_NEEDLE_LTR_BACK, state);
}

void patternFront()
{

  // react only if there is new cursorposition
  if (currentCursorPositionLast != currentCursorPosition)
  {

    // RTL
    if (currentDirection == DIRECTION_RIGHT_LEFT)
    {
      int patternPositionRTL = currentCursorPosition - (firstNeedle + offsetCarriage_RTL);
      // set needles in absolute position
      if (patternPositionRTL > 0 && patternPositionRTL <= patternLength * 2)
      {
        setNeedle_RTL(knitPattern[((patternLength * 2 - patternPositionRTL) / 2)]);
      }
      else
      {
        setNeedle_RTL(1);
      }
      // send pattern End
      if (patternPositionRTL == patternLength * 2 + 1)
      {
        sendCommand(COM_CMD_PATTERN_END, "1");
      }
    }

    // LTR
    if (currentDirection == DIRECTION_LEFT_RIGHT)
    {

      int patternPositionLTR = currentCursorPosition - (firstNeedle + offsetCarriage_LTR);
      if (patternPositionLTR > 0 && patternPositionLTR <= patternLength * 2)
      {
        setNeedle_LTR(knitPattern[((patternLength * 2 - patternPositionLTR) / 2)]);
      }
      else
      {
        setNeedle_LTR(1);
      }
      // send pattern End
      if (patternPositionLTR == 0)
      {
        sendCommand(COM_CMD_PATTERN_END, "1");
      }
    }

    // store last CursorPosition
    currentCursorPositionLast = currentCursorPosition;
  }
}

void interruptPinChangeEncoder()
{

  unsigned long now = micros();
  if (now - lastCursorChange < 1000)
  {
    lastCursorChange = now;
    return;
  }
  lastCursorChange = now;

  currentPinChangeValue = digitalRead(PIN_CSENSE);
  currentPinChangeOppositeValue = digitalRead(PIN_CREF);

  //    Serial.print(String(0+currentPinChangeValue));
  //    Serial.print("-");
  //    Serial.println(String(0+currentPinChangeOppositeValue));

  // Determine direction
  if (currentPinChangeValue == currentPinChangeOppositeValue)
  { // ef sama þá vinstri ti hægri
    currentDirection = DIRECTION_LEFT_RIGHT;
  }
  else
  {
    currentDirection = DIRECTION_RIGHT_LEFT;
  }

  // RTL = 1, LTR = -1
  currentCursorPosition += currentDirection;

  // AutoCalibrate
  passapCalibrateArray[passapCalibratePointer & 0x07] = currentPinChangeValue;
  passapCalibrateArray[(passapCalibratePointer + 1) & 0x07] = currentPinChangeOppositeValue;
  /*
  // uncomment for finding the calibration sequence -> store in 'passaptestpattern'
    for (int i = 0; i < 8; i++) {

      if ((passapCalibratePointer - i) >= -1) {

        Serial.print(passapCalibrateArray[(passapCalibratePointer - i+1)]);

      }
      else {

       Serial.print(passapCalibrateArray[(passapCalibratePointer - i+9)]);

      }
    }
  Serial.println("");
  */
  //
  int found = 1;
  for (int i = 0; i < 8; i++)
  {

    if ((passapCalibratePointer - i) >= -1)
    {

      // Serial.print((passapCalibratePointer - i+1));
      if (passapCalibrateArray[(passapCalibratePointer - i + 1) & 0x07] !=
          passaptestpattern[i])
      {
        found = 0;
        break;
      }
    }
    else
    {

      //  Serial.print((passapCalibratePointer - i + 9));
      if (passapCalibrateArray[(passapCalibratePointer - i + 9) & 0x07] !=
          passaptestpattern[i])
      {
        found = 0;
        break;
      }
    }
  }

  // Serial.println("end");
  if (found)
  {
    sendCommand(COM_CMD_RESPONSE, "fc");
    // calibrate
    currentCursorPosition = -2;
  }
  /*
    Serial.print("point:");
    Serial.println(passapCalibratePointer);
    Serial.println("");
  */
  passapCalibratePointer = passapCalibratePointer + 2;
  if (passapCalibratePointer >= 8)
  {
    passapCalibratePointer = 0;
  }
}

void patternBack()
{
  // react only if there is new cursorposition
  if (currentCursorPositionLast_back != currentCursorPosition_back)
  {

    // RTL
    if (currentDirection_back == DIRECTION_RIGHT_LEFT)
    {
      int patternPositionRTL_back = currentCursorPosition_back - (firstNeedle + offsetCarriage_RTL_back);
      // set needles in absolute position
      if (patternPositionRTL_back > 0 && patternPositionRTL_back <= patternLength * 2)
      {
        setNeedle_RTL_back(knitPattern_back[((patternLength * 2 - patternPositionRTL_back) / 2)]);
      }
      else
      {
        setNeedle_RTL_back(1);
      }
      //      //send pattern End
      //      if (patternPositionRTL_back == patternLength*2+1 ){
      //        sendCommand(COM_CMD_PATTERN_END_back, "1");
      //      }
    }

    // LTR
    if (currentDirection_back == DIRECTION_LEFT_RIGHT)
    {

      int patternPositionLTR_back = currentCursorPosition_back - (firstNeedle + offsetCarriage_LTR_back);
      if (patternPositionLTR_back > 0 && patternPositionLTR_back <= patternLength * 2)
      {
        setNeedle_LTR_back(knitPattern_back[((patternLength * 2 - patternPositionLTR_back) / 2)]);
      }
      else
      {
        setNeedle_LTR_back(1);
      }
      //      //send pattern End
      //      if (patternPositionLTR_back == 0){
      //        sendCommand(COM_CMD_PATTERN_END, "1");
      //      }
    }

    // store last CursorPosition
    currentCursorPositionLast_back = currentCursorPosition_back;
  }
}

void interruptPinChangeEncoder_back()
{

  unsigned long now = micros();
  if (now - lastCursorChange_back < 1000)
  {
    lastCursorChange_back = now;
    return;
  }
  lastCursorChange_back = now;

  currentPinChangeValue_back = digitalRead(PIN_CSENSE_BACK);
  currentPinChangeOppositeValue_back = digitalRead(PIN_CREF_BACK);
  /*
  Serial.print(String(0 + currentPinChangeValue_back));
  Serial.print("-");
  Serial.println(String(0 + currentPinChangeOppositeValue_back));
  */

  // Determine direction
  if (currentPinChangeValue_back == currentPinChangeOppositeValue_back)
  {
    //    currentDirection_back = DIRECTION_LEFT_RIGHT;
    currentDirection_back = DIRECTION_RIGHT_LEFT;
  }
  else
  {
    //      currentDirection_back = DIRECTION_RIGHT_LEFT;
    currentDirection_back = DIRECTION_LEFT_RIGHT;
  }

  // RTL = 1, LTR = -1
  currentCursorPosition_back += currentDirection_back;

  // AutoCalibrate
  passapCalibrateArrayBack[passapCalibratePointerBack & 0x07] = currentPinChangeValue_back;
  passapCalibrateArrayBack[(passapCalibratePointerBack + 1) & 0x07] = currentPinChangeOppositeValue_back;

  /*
  // uncomment for finding the calibration sequence -> store in 'passaptestpatternBack'
    for (int i = 0; i < 9; i++) {

      if ((passapCalibratePointerBack - i) >= -1) {

        Serial.print(passapCalibrateArrayBack[(passapCalibratePointerBack - i+1)]);

      }
      else {

       Serial.print(passapCalibrateArrayBack[(passapCalibratePointerBack - i+9)]);

      }
    }
  Serial.println("");
    */
  int found = 1;
  for (int i = 0; i < 9; i++)
  {

    if ((passapCalibratePointerBack - i) >= -1)
    {

      //  Serial.print((passapCalibratePointerBack - i+1));
      if (passapCalibrateArrayBack[(passapCalibratePointerBack - i + 1) & 0x07] !=
          passaptestpatternBack[i])
      {
        found = 0;
        break;
      }
    }
    else
    {

      //  Serial.print((passapCalibratePointerBack - i + 9));
      if (passapCalibrateArrayBack[(passapCalibratePointerBack - i + 9) & 0x07] !=
          passaptestpatternBack[i])
      {
        found = 0;
        break;
      }
    }
  }

  //  Serial.println("end");
  if (found)
  {
    sendCommand(COM_CMD_RESPONSE, "bc");
    // calibrate back
    currentCursorPosition_back = -2;
  }
  /*
    Serial.print("point:");
    Serial.println(passapCalibratePointerBack);
    Serial.println("");
  */
  passapCalibratePointerBack = passapCalibratePointerBack + 2;
  if (passapCalibratePointerBack >= 8)
  {
    passapCalibratePointerBack = 0;
  }
}

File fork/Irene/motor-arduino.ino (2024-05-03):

/* Project "Passap-E6000-hacked-and-rebuilt", Version 6, 20.6.2021
 *  Part: Motor Controller Electra 4600, Passap E6000
 *  project published under Hackaday
 *  https://hackaday.io/project/163701-passap-e6000-rebuilt-and-replaced-console 
 *  created by Irene Wolf
*/


#include <Wire.h>
#include <MCP23017.h>     // https://github.com/wollewald/MCP23017_WE
#include "CmdMessenger.h"


#define Serial Serial
// max baudrate for nano
const int BAUD_RATE = 19200;
CmdMessenger c = CmdMessenger(Serial, ',', ';', '/');


// Potentiometer
#define PIN_POTI                       A6      // input potentiometer

// RJ45 (straight trough)
#define PIN_COLOURCHANGE               4       // change colour
#define PIN_DIRECTION_CHANGE_RIGHT     3       // changes direction from left to right
#define PIN_DIRECTION_CHANGE_LEFT      10      // changes direction from right to left
#define PIN_FREQUENCY                  6       // frequency FU
#define PIN_DRIVE                      7       // drive
#define PIN_DIRECTION_FU               5       // input from FU, feedback direction RTL, LTR, 0 = forward, 1 = backward
#define PIN_RESET_FU                   8
#define PIN_EMERGENCY_STOPP            9       // input Pin

#define PIN_RESET_MCP                  11      // not in use


///////////////////////////////////////////////////////////////////////////////

//constant and variables Arduino - mcp 23017 - Raspberry Pi --> Motor Electra 4600

///////////////////////////////////////////////////////////////////////////////

#define MCP_ADDRESS 0x20 // (A2/A1/A0 = LOW) 

#define MCP_IODIRA  0x00  // I/O direction register
#define MCP_IODIRB  0x01

#define MCP_GPINTENA 0x04 // Interrupt-on-change pins A
#define MCP_GPINTENB 0x05 // Interrupt-on-change pins B

#define MCP_DEFVALA 0x06  // Default value register A
#define MCP_DEFVALB 0x07

#define MCP_INTCONA 0x08  // Interrupt-on-change control register A
#define MCP_INTCONB 0x09

#define MCP_INTCAPA 0x10  // Interrupt captured value for port register A
#define MCP_INTCAPB 0x11  // Interrupt captured value for port register B

#define MCP_IOCONA 0x0A   // I/O expander configuration register A
#define MCP_IOCONB 0x0B

#define MCP_GPPUA 0x0C    // GPIO pull-up resistor register A
#define MCP_GPPUB 0x0D

#define MCP_GPIOA 0x12    // General purpose I/O port register A
#define MCP_GPIOB 0x13    // General purpose I/O port register B

#define MCP_OLATA 0x14    // Output latch register 0 A
#define MCP_OLATB 0x15    // Output latch register 0 B

#define MCP23017_INT_ERR 255 // Interrupt error

// USB CmdMessenger commands, communication between Arduino and Raspberry Pi --> console
enum {
  slowDownSpeed, 
  sbSlowDownSpeed,
  setColourChange, 
  sbColourChange,
  setRowEndStopp, 
  sbRowEndStopp,
  setFormStopp,
  sbFormStopp,
  setDrive_left, 
  sbDrive_left,
  setDrive_right, 
  sbDrive_right,
};


// mcp23017 interrupt arduino
int interruptPin = 2;
volatile bool event;
volatile bool flag;
byte intCapReg;

// button state motor controller
volatile boolean state_drive;
volatile boolean state_driveLeft;
volatile boolean state_driveRight;
volatile boolean state_endStopp;
volatile boolean state_colourChange;
volatile boolean state_Reset;
volatile boolean flag_endStopp_left;
volatile boolean flag_endStopp_right;

// LED motor controller
int drive_LED = 0;              // red
int drive_left_LED = 1;         // white-yellow
int drive_right_LED = 2;        // white
int endStopp_LED = 3;           // green
int colourChange_LED = 4;       // yellow
int reset_LED = 5;              // blue

// value potentiometer
int analogValue;
int valuePoti;
volatile int statePoti;


/*
 * You can choose if you want to use the reset function or not.
 * If you don't need it, you can save one pin.
 */
MCP23017 myMCP(MCP_ADDRESS,11); // Pin 11 is used as reset pin
//MCP23017 myMCP(MCP_ADDRESS); // alternative option not using the reset pin


/////////////////////////////

// Interrupt routine, mcp23017 --> Arduino

////////////////////////////


// flag is reset when the interrupt has been processed 
// all interrupts are ignored until then 
void eventHappened(){
  if (flag == true){ 
    event = true;
    flag = false;
  }
}

// resets both flags
void cleanInterrupt(){
  event = false;
  flag = true;
  EIFR=0x01; 
}


/* when a button is pressed, an interrupt is triggered
 *   depending on which button was pressed the correspondending
 *      - LED is set
 *      - the state of the output pin Arduino is changed
 *      - a function is called 
*/
        
void handleInterrupt(){

  byte intFlagReg, eventPin; 
  
    intFlagReg = myMCP.getIntFlag(B);
    eventPin = log(intFlagReg)/log(2);

    intCapReg = myMCP.getIntCap(B);
    
    
    // drive or stopp
    switch(eventPin){
      case 0: {  // red button & LED, drive
        if(intFlagReg == 1){
          state_drive = !state_drive; 
          mcp_digitalWrite(drive_LED, state_drive);
          
          digitalWrite(PIN_DRIVE, state_drive);
          }

          if(state_drive == HIGH){
          mcp_digitalWrite(reset_LED, LOW);
          }                
      }
      break;
      
      // white_y button & LED, drive left
      // the intFlagReg ensures that the signal is only processed once when there is a change of direction. 
      case 1: {  
        if(intFlagReg==2){
          drive_left();    
        }
      }
      
      // white button & LED, drive right 
      break;
      case 2:{   
        if(intFlagReg==4){
        drive_right();      
        } 
      }           
      break;
      
      // yellow button & LED
      // colour change, the lock moves into the color changer 
      case 4:{   
        if(intFlagReg==16){
          state_colourChange = !state_colourChange;
          mcp_digitalWrite(colourChange_LED, state_colourChange);
          digitalWrite(PIN_COLOURCHANGE, !state_colourChange);   // Low means override
        }
      }
      break;
      
      // green button & LED, end stopp
      // lock stops at the end of the knitted row
      case 3:{   
        if(intFlagReg==8){
          state_endStopp = !state_endStopp;
          mcp_digitalWrite(endStopp_LED, state_endStopp);
          
        }
      }
      break;
      
      // blue button & LED
      // resets the FU
      case 5:{  
        if(intFlagReg == 32){
          mcp_digitalWrite(reset_LED, HIGH);
          digitalWrite(PIN_RESET_FU, HIGH);
          delay(50);
          digitalWrite(PIN_RESET_FU, LOW);
  
          if(digitalRead(PIN_EMERGENCY_STOPP) == LOW){
            state_drive = LOW;   
            mcp_digitalWrite(drive_LED, state_drive);  
          }
        
          drive_right();
          drive_left();
        }
      }
      break;

      default: break;     
    } 
    
    // resets the interrupt flag
    cleanInterrupt();
}


/////////////////////////////

// function mcp 23017, placed in motor controller

////////////////////////////

// Register: Bank A all LED
// Register: Bank B all button
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

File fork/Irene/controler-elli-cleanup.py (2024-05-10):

# Passap E6000 rebuilt and replaced console,
# Passap Electra 4600 rebuilt and replaced controller

# created by Irene Wolf
# hreinskrifað af Elíasi Lúðvíkssyni
# Notobene að ég get ekki lagfært allt þar sem ég
# 	er bara með aðgang að kóðanum en ekki hardware
# Öll output verða því að halda sér eins og þau eru þó ég dragi þau í efa

# Version 36.3, 23.7.2021
# Python code for Raspberry Pi 3, OS Debian Buster

# Importum bara öllu sem hún importaði

import random, sys
import PyCmdMessenger
import struct
import RPi.GPIO as GPIO
import sqlite3
import time
import datetime
import os


from PyQt5.QtWidgets import QApplication, QMainWindow, QVBoxLayout, QGridLayout, QAction
from PyQt5.QtWidgets import QWidget, QLineEdit, QMessageBox, QLabel, QFileDialog, QDialog
from PyQt5.QtGui import QFont, QColor
from PyQt5.QtCore import pyqtSlot
from PyQt5 import QtCore, QtWidgets, QtGui

import csv

from PIL import Image

# Bætum við numpy fyrir fylkja breytingar

import numpy as np

# --------------------------------------------------------------------------
# Setup Pin for interrupt
# --------------------------------------------------------------------------

# GPIO Pin to get signals form Arduino front lock
right_GPIO = 7
left_GPIO = 11
directionchange_GPIO = 13

GPIO.setmode(GPIO.BOARD)

GPIO.setup(right_GPIO, GPIO.IN, pull_up_down=GPIO.PUD_DOWN)
GPIO.setup(left_GPIO, GPIO.IN, pull_up_down=GPIO.PUD_DOWN)
GPIO.setup(directionchange_GPIO, GPIO.IN, pull_up_down=GPIO.PUD_DOWN)
# Útskýring fyrir pull down og pull up
# An input gpio will float between 0 and 1 if it's not connected to a voltage.

# The pull-up/downs supply that voltage so that the gpio will have a defined value UNTIL overridden by a stronger force.

# You should set a pull-down (to 0) when you expect the stronger force to pull it up to 1.

# You should set a pull-up (to 1) when you expect the stronger force to pull it down to 0.

# Otherwise the gpio will not change state and you'll never know about the external event.

# -----------------------------------------------------------------------------
# Variables
# -----------------------------------------------------------------------------

# Ég mun setja in variables hérna eftir þörf en ég dreg þær allar stranglega í efa

countTech = 0
tech_Array = []
# count knitted row
rowCount = 0
# count knitted row VNB, HNB
rowCount_VNB = 0
rowCount_HNB = 0

#--------------------------------------------------------------------------
# Communication Arduino - Raspi
#--------------------------------------------------------------------------

motor = PyCmdMessenger.ArduinoBoard('/dev/ttyUSB-ArduinoMotor',baud_rate=19200)
motor.enable_dtr=False
motor.int_bytes=4

commands =[["slowDownSpeed", "i"],["sbSlowDownSpeed", "i"],
           ["setColourChange", "?"],["sbColourChange", "?"],
           ["setRowEndStopp", "?"],["sbRowEndStopp", "?"],
           ["setFormStopp", ""],["sbFormStopp", "s"],
           ["setDrive_left", ""], ["sbDrive_left", "s"],
           ["setDrive_right",""], ["sbDrive_right", "s"]]

connectionMotor= PyCmdMessenger.CmdMessenger(motor,commands)

# connect to VNB Arduino M0 (front lock)
a = PyCmdMessenger.ArduinoBoard('/dev/ttyUSB-ArduinoVNB',115200)
a.enable_dtr=False
a.int_bytes=4
connectionVNB = PyCmdMessenger.CmdMessenger(a, [["sPat", "b*"],["sbPat", "b*"],
                                             ["setEmptyPat", "b*"], ["sbEmptyPat", "b*"],
                                             ["setNPos", "l"],["sbNPos", "l*"],
                                             ["getNPos", ""],["sendNPos", "l"],   
                                             ["setLeEnd", "i"], ["sbLeEnd", "l"],
                                             ["setRiEnd", "i"], ["sbRiEnd", "l"],
                                             ["getCursorPos", ""], ["sendCursorPos", "l"],                                           
                                             ])


# connect to HNB Arduino M0 Pro (back lock)
b = PyCmdMessenger.ArduinoBoard('/dev/ttyUSB-ArduinoHNB',115200)
b.enable_dtr=False
b.int_bytes=4
connectionHNB = PyCmdMessenger.CmdMessenger(b, [["sPat", "b*"],["sbPat", "b*"],
                                             ["setEmptyPat", "b*"], ["sbEmptyPat", "b*"],                                              
                                             ["setNPos", "l"],["sbNPos", "l*"],  
                                             ["getNPos", ""],["sendNPos", "l"],  
                                             ["setLeEnd", "i"], ["sbLeEnd", "l"],
                                             ["setRiEnd", "i"], ["sbRiEnd", "l"],
                                             ])    
def pattern_Array(listMy):
	patternArray = np.zeros(listMy.shape[0],23)
	for x in range(0,listMy.shape[0]):

		pattern = np.full((1,23),0b0)

		for m in range(0,22): # Hér er mögulega eh rugl þar sem pattern hefur lengdina 23, range(0,23) mundi þá ítra allt
			for y in range(0,8):
				n = y + m*7
				if listMy[x,n] == 0:
					pattern[0,m] = pattern[0,m].__lshift__(1)
				else:
					pattern[0,m] = pattern
		patternArray[x] = pattern
	return patternArray

def get_pattern(data):
	filename = Image.open(data)
	widthMy = filename.size[0]
	heightMy = filename.size[1]
	const0 = np.zeros((heightMy,widthMy))
	black = const0
	white = const0
	green = const0
	blue = const0
	red = const0
	for x in range(0, heightMy):
		for y in range(0, widthMy):
			pixel = (y, x)
			redMy, greenMy, blueMy = filename.getpixel(pixel)
			black[x,y] = int(redMy == 0 and greenMy == 0 and blueMy == 0)
			white[x,y] = int(redMy == 255 and greenMy == 255 and blueMy == 255)
			green[x,y] = int(redMy < 20 and greenMy > 200 and blueMy < 20)
			blue[x,y] = int(redMy < 20 and greenMy < 20 and blueMy > 200)
			red[x,y] = int(redMy > 200 and greenMy < 20 and blueMy < 20)
	return ( pattern_Array(black),  # Trúi ekki að þetta sé nauðsyn
		 pattern_Array(white), 
		 pattern_Array(green), 
		 pattern_Array(blue),
		 pattern_Array(red),
		 pattern_Array(black+white),
		pattern_Array(black+green),
		pattern_Array(black+blue),
		pattern_Array(black+red),
		pattern_Array(black+white+green),
		pattern_Array(black+white+blue),
		pattern_Array(black+white+red),
		pattern_Array(black+green+blue),
		pattern_Array(black+green+red),
		pattern_Array(black+blue+red),
		pattern_Array(white+green),
		pattern_Array(white+blue),
		pattern_Array(white+red),
		pattern_Array(white+green+blue),
		pattern_Array(white+green+red),
		pattern_Array(white+blue+red),
		pattern_Array(green+blue),
		pattern_Array(green+red),
		pattern_Array(green+blue+red),
		pattern_Array(blue+red)
	)



def get_needlePos_VNB():
	connectionVNB.send("getNpos")
	received_VNB = connectionVNB.receive()
	return received_VNB[1][0]

def get_needlePos_HNB():
	connectionMotor.send("getNpos")
	received_VNB = connectionVNB.receive()
	return received_VNB[1][0]

def drive_left():
	connectionMotor.send("setDrive_left")
	received_Motor = connectionMotor.receive()
	return received_Motor[1][0]
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

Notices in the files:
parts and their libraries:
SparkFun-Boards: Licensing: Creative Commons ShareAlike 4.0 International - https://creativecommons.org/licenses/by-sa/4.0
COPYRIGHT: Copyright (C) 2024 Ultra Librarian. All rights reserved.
